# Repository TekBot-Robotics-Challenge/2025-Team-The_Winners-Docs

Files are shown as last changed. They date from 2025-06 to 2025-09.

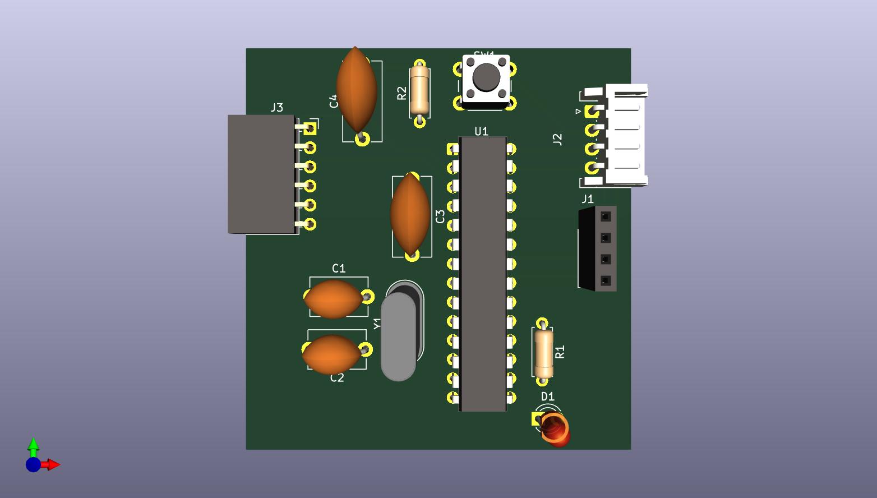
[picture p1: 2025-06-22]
Tekbot_The_Winners/electonic/test2/kicad/black_box/Test_2.jpg

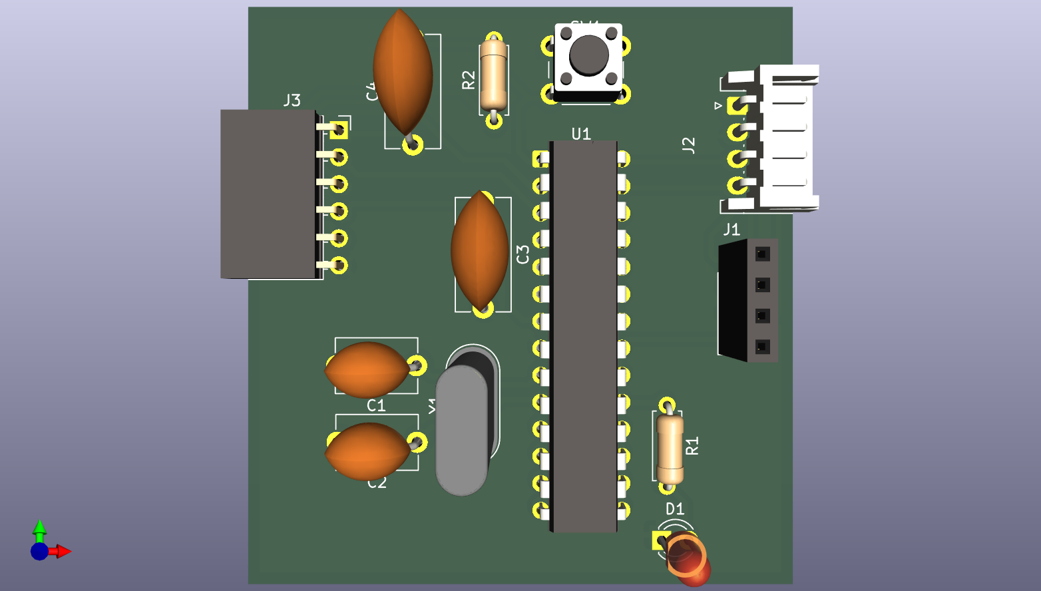
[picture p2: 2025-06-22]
Tekbot_The_Winners/electonic/test2/kicad/black_box/Test_2.png

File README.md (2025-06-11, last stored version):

# Website

This website is built using [Docusaurus](https://docusaurus.io/), a modern static website generator.

## Installation

```bash
yarn
```

## Local Development

```bash
yarn start
```

This command starts a local development server and opens up a browser window. Most changes are reflected live without having to restart the server.

## Build

```bash
yarn build
```

This command generates static content into the `build` directory and can be served using any static contents hosting service.

## Deployment

Using SSH:

```bash
USE_SSH=true yarn deploy
```

Not using SSH:

```bash
GIT_USER=<Your GitHub username> yarn deploy
```

If you are using GitHub pages for hosting, this command is a convenient way to build the website and push to the `gh-pages` branch.
"# Mise … jour" 
"Relance d‚ploiement" 
"Relance d‚ploiement"

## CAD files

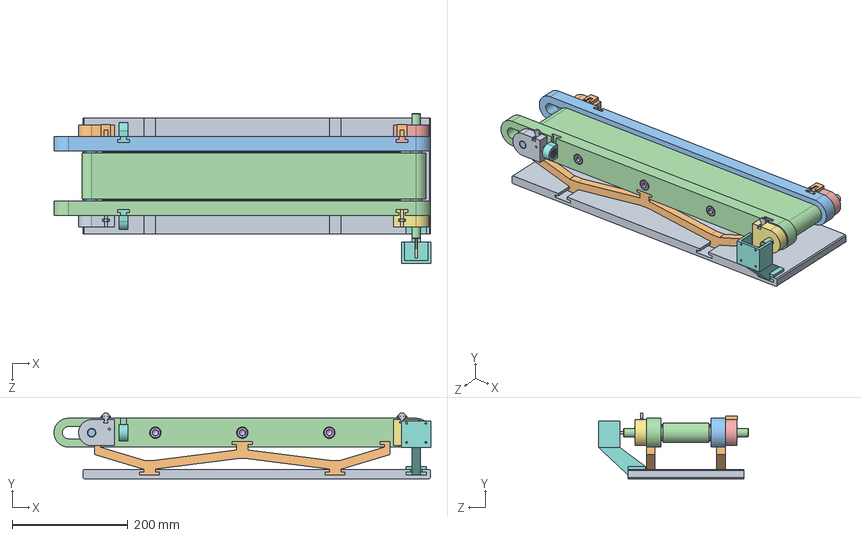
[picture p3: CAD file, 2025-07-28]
Tekbot_The_Winners/mechanic/testfinal/Assemblage2Finalconvoyeur2022.SLDASM
650.4 x 113.0 x 259.0 mm
Base
Pièce W x 2
Support lateral - Gauche
Support lateral DROIT
Palier arbre de renvoi
radial ball bearing_68_iso x 4
Palier arbre de renvoi 2
Support Tendeur 1 x 2
Palier simple coté moteur
Palier simple coté moteur 2
Tambour de renvoi
Tambour de commande
Plaque de mantient
socket head cap screw_iso x 6
Arbre du moteur
Support moteur
Boitier LDR x 2
boitier laser x 2
Dague tendeur x 2
Courroie1-1^Assemblage2Finalconvoyeur

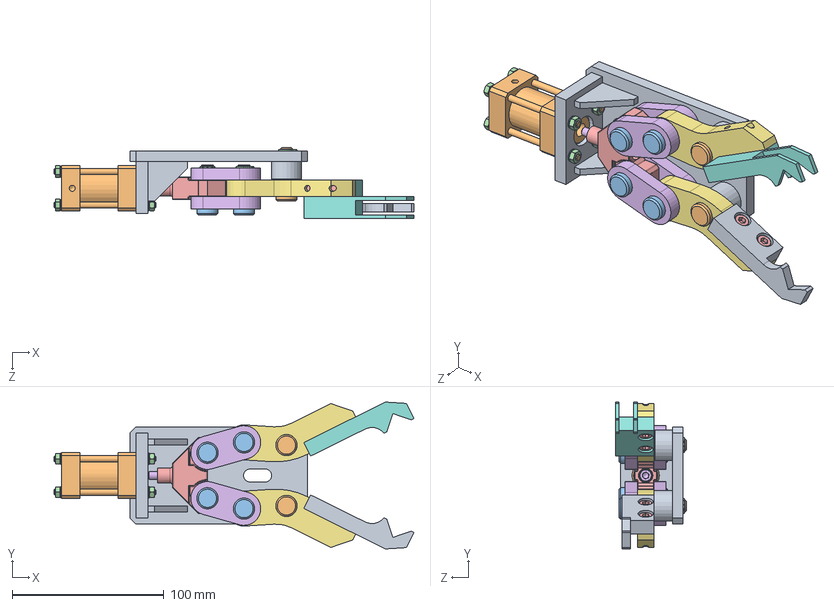
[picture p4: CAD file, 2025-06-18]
Tekbot_The_Winners/mechanic/test1/Assemblage Niveau Débutant/assemblage pince_me.SLDASM
236.9 x 96.7 x 47.0 mm
Corps
Corps verin
rondelle w4 x 8
Ecrou H M4 x 8
Embout de verin
Biellette x 4
Porte machoire x 2
Machoire gauche
Machoire droite
Axe de porte machoire x 2
Axe de biellette x 4
Circlips x 6
socket head cap screw_iso x 4
vis CHC M5x25

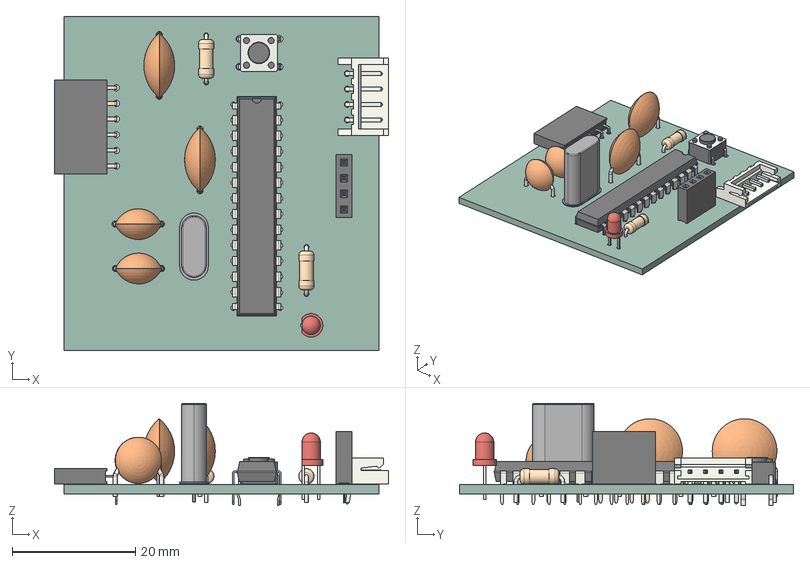
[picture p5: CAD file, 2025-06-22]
Tekbot_The_Winners/electonic/test2/kicad/black_box/Test_2.step
54.2 x 54.2 x 16.6 mm
LED_D3.0mm
JST_EH_S4B-EH_1x04_P2.50mm_Horizontal
C_Disc_D10.5mm_W5.0mm_P10.00mm x 2
PinSocket_1x04_P2.54mm_Vertical
C_Disc_D7.5mm_W5.0mm_P7.50mm x 2
R_Axial_DIN0207_L6.3mm_D2.5mm_P7.62mm_Horizontal x 2
SW_PUSH_6mm
DIP-28_W7.62mm
Crystal_HC49-U_Vertical
PinSocket_1x06_P2.54mm_Horizontal
Test_2_PCB

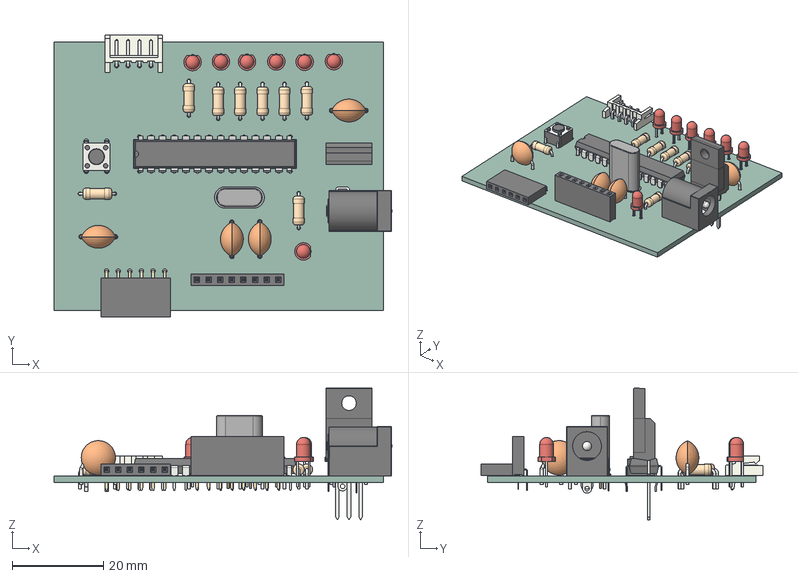
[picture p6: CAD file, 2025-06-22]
Tekbot_The_Winners/electonic/test2/kicad/station_control/Test_22.step
73.9 x 61.6 x 28.9 mm
Crystal_HC49-U_Vertical
R_Axial_DIN0207_L6.3mm_D2.5mm_P7.62mm_Horizontal x 8
SW_PUSH_6mm
C_Disc_D7.5mm_W5.0mm_P7.50mm x 4
LED_D3.0mm x 7
BarrelJack_Horizontal
PinSocket_1x08_P2.54mm_Vertical
DIP-28_W7.62mm
JST_EH_S4B-EH_1x04_P2.50mm_Horizontal
TO-220F-3_Vertical
PinSocket_1x06_P2.54mm_Horizontal
Test_22_PCB

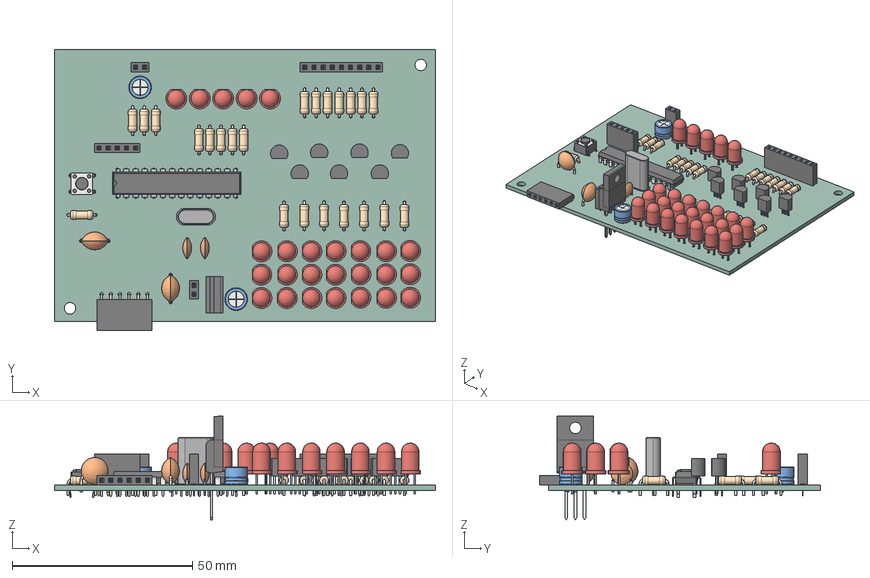
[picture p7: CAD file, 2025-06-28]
Tekbot_The_Winners/electonic/test3/KiCad/Test_3.step
105.7 x 77.9 x 28.9 mm
R_Axial_DIN0207_L6.3mm_D2.5mm_P7.62mm_Horizontal x 23
TO-92_Inline x 7
PinSocket_1x02_P2.54mm_Vertical x 2
PinSocket_1x06_P2.54mm_Horizontal
LED_D5.0mm x 26
C_Radial_D6.3mm_H5.0mm_P2.50mm x 2
C_Disc_D7.5mm_W5.0mm_P7.50mm x 2
TO-220F-3_Vertical
C_Disc_D6.0mm_W2.5mm_P5.00mm x 2
Crystal_HC49-U_Vertical
PinSocket_1x05_P2.54mm_Vertical
SW_PUSH_6mm
DIP-28_W7.62mm
PinSocket_1x09_P2.54mm_Vertical
Test_3_PCB

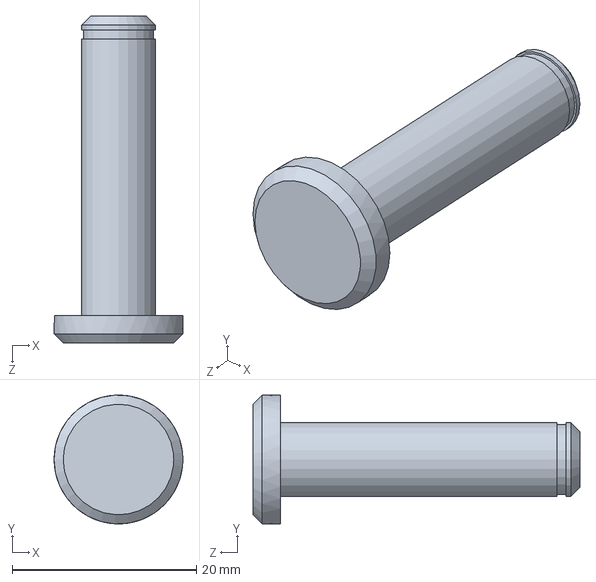
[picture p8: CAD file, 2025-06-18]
Tekbot_The_Winners/mechanic/test1/Assemblage Niveau Débutant/Axe de porte machoire.SLDPRT
14.0 x 14.0 x 35.5 mm

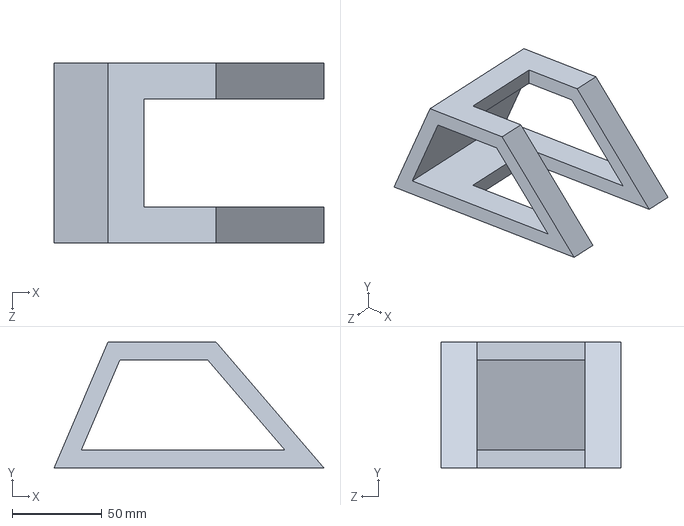
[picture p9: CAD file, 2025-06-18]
Tekbot_The_Winners/mechanic/test1/piece3.SLDPRT
150.0 x 70.0 x 100.0 mm

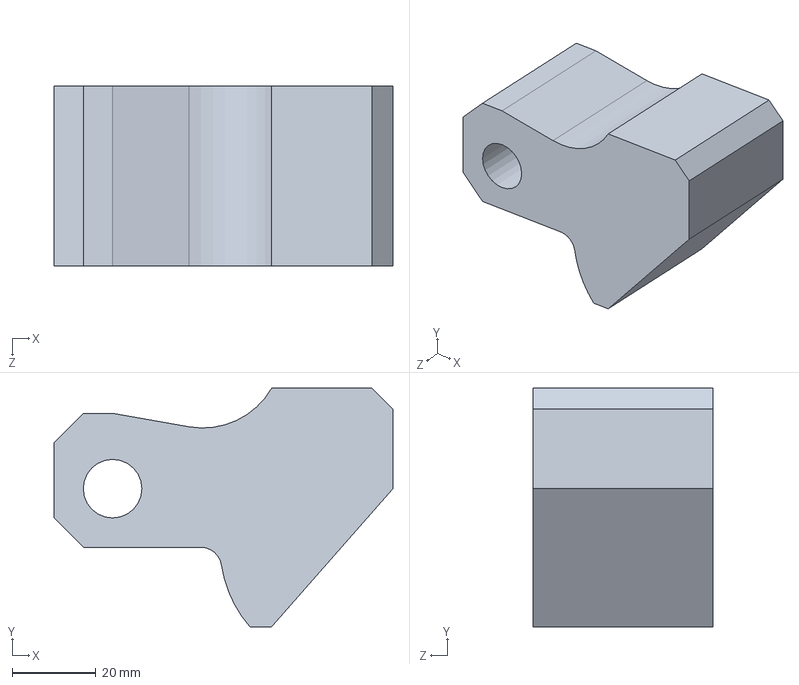
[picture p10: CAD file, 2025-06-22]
Tekbot_The_Winners/mechanic/test2/Partie1_Cas 1.SLDPRT
81.0 x 57.0 x 43.0 mm

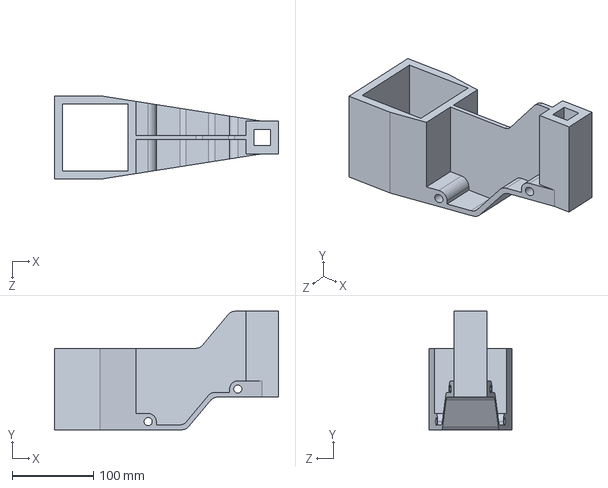
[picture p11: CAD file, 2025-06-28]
Tekbot_The_Winners/mechanic/test3/TEST3_Cas_2.SLDPRT
275.0 x 145.5 x 102.5 mm

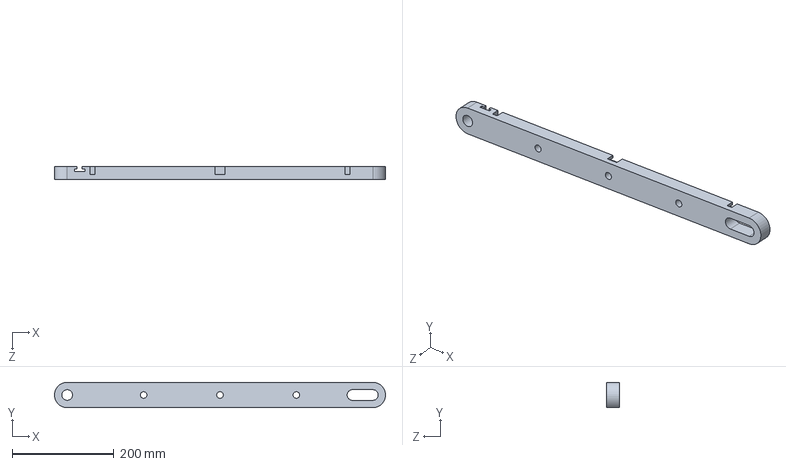
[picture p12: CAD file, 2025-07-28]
Tekbot_The_Winners/mechanic/testfinal/Support lateral - Gauche.SLDPRT
649.8 x 50.0 x 25.0 mm

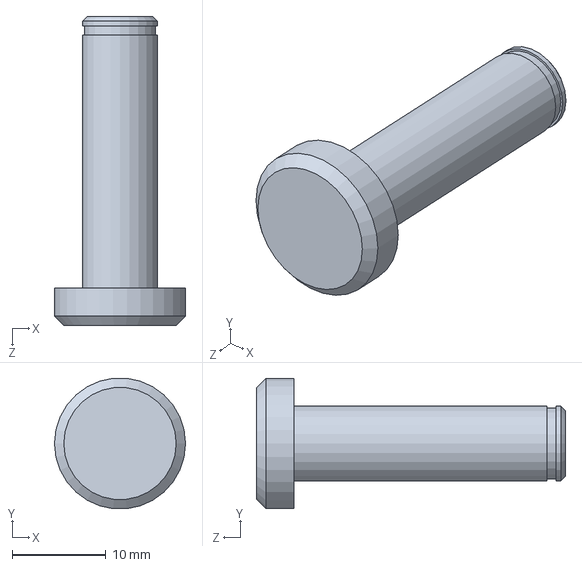
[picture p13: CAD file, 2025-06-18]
Tekbot_The_Winners/mechanic/test1/Assemblage Niveau Débutant/Axe de biellette.SLDPRT
14.0 x 13.9 x 33.0 mm

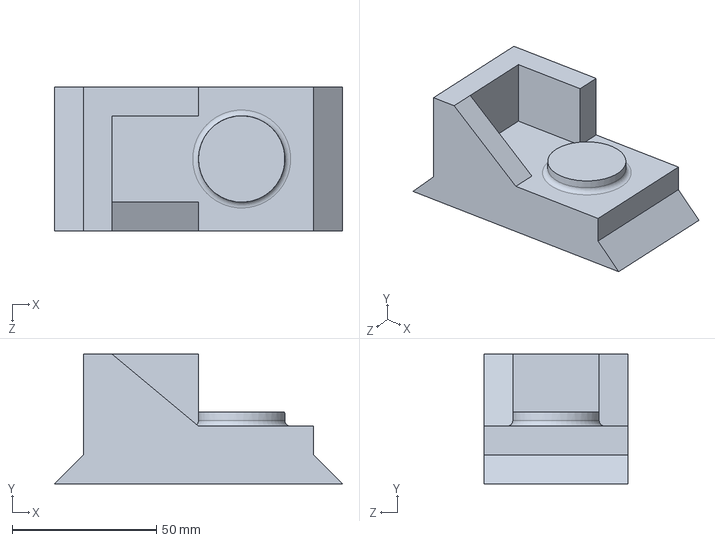
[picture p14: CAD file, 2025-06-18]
Tekbot_The_Winners/mechanic/test1/piece4.SLDPRT
100.0 x 45.0 x 50.0 mm

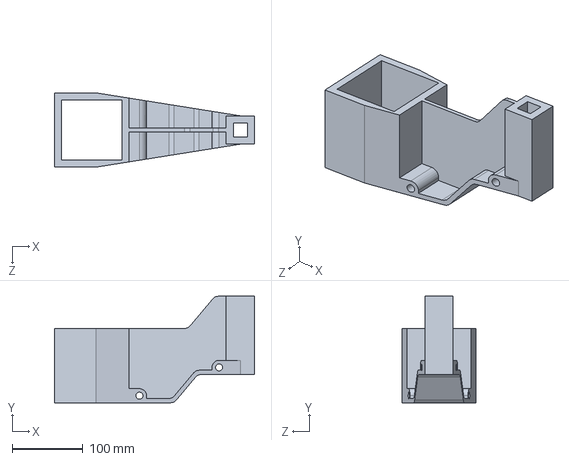
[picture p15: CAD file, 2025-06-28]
Tekbot_The_Winners/mechanic/test3/TEST3_Cas_3.SLDPRT
282.5 x 150.5 x 105.0 mm

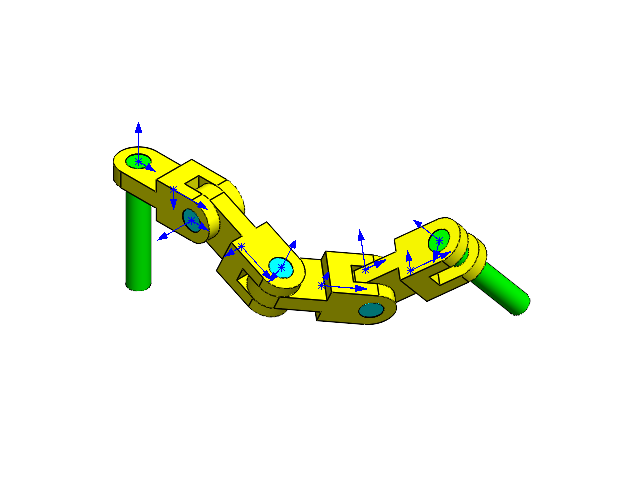
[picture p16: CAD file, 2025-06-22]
Tekbot_The_Winners/mechanic/test2/Assemblage 2_a.SLDASM
long_pin x 2
chain_link x 4
short_pin x 3

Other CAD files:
Tekbot_The_Winners/mechanic/test2/Assemblage 2_b.SLDASM
Tekbot_The_Winners/mechanic/testfinal/Moteur1.SLDASM
Tekbot_The_Winners/mechanic/test1/Assemblage Niveau Débutant/assemblage pince.SLDASM
Tekbot_The_Winners/mechanic/testfinal/Assemblage2Finalconvoyeur.SLDASM
Tekbot_The_Winners/mechanic/test1/Assemblage Niveau Débutant/Biellette.SLDPRT
Tekbot_The_Winners/mechanic/test1/Assemblage Niveau Débutant/Circlips.SLDPRT
Tekbot_The_Winners/mechanic/test1/Assemblage Niveau Débutant/Corps verin.SLDPRT
Tekbot_The_Winners/mechanic/test1/Assemblage Niveau Débutant/Corps.SLDPRT
Tekbot_The_Winners/mechanic/test1/Assemblage Niveau Débutant/Ecrou H M4.SLDPRT
Tekbot_The_Winners/mechanic/test1/Assemblage Niveau Débutant/Embout de verin.SLDPRT
Tekbot_The_Winners/mechanic/test1/Assemblage Niveau Débutant/Machoire droite.SLDPRT
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

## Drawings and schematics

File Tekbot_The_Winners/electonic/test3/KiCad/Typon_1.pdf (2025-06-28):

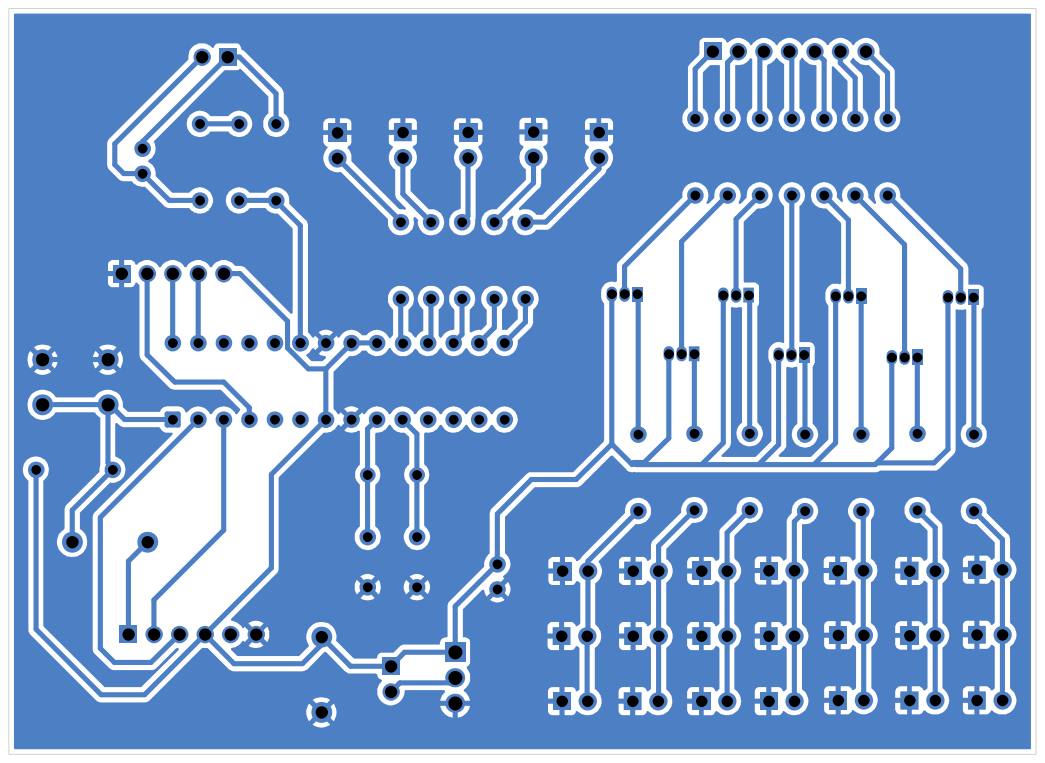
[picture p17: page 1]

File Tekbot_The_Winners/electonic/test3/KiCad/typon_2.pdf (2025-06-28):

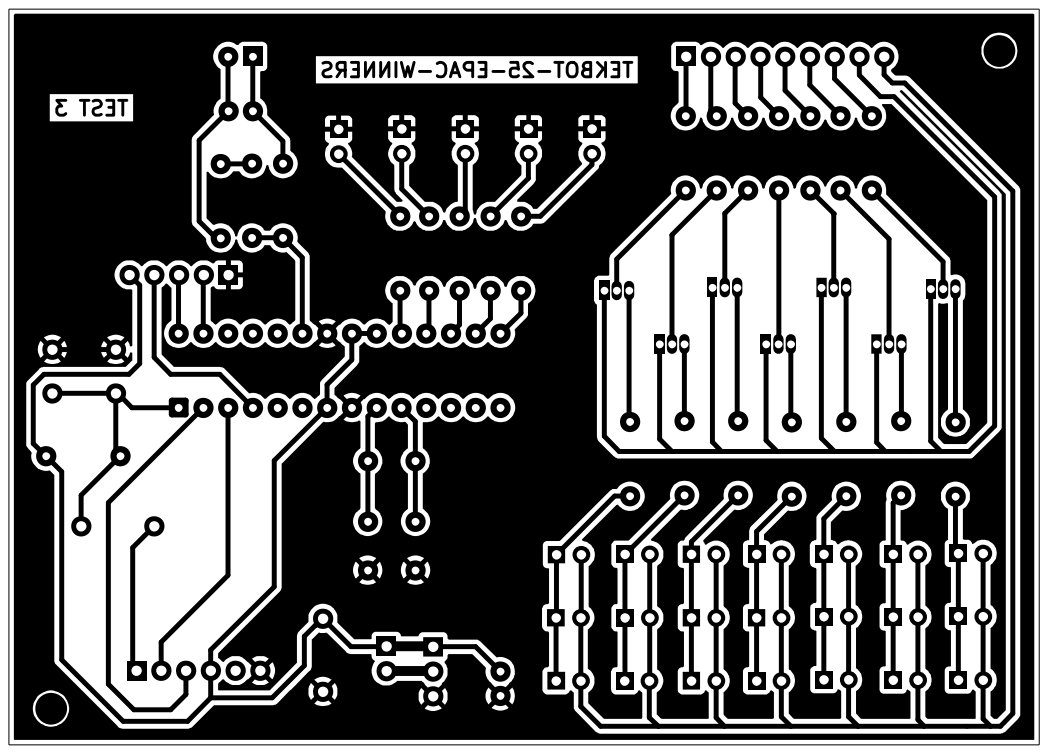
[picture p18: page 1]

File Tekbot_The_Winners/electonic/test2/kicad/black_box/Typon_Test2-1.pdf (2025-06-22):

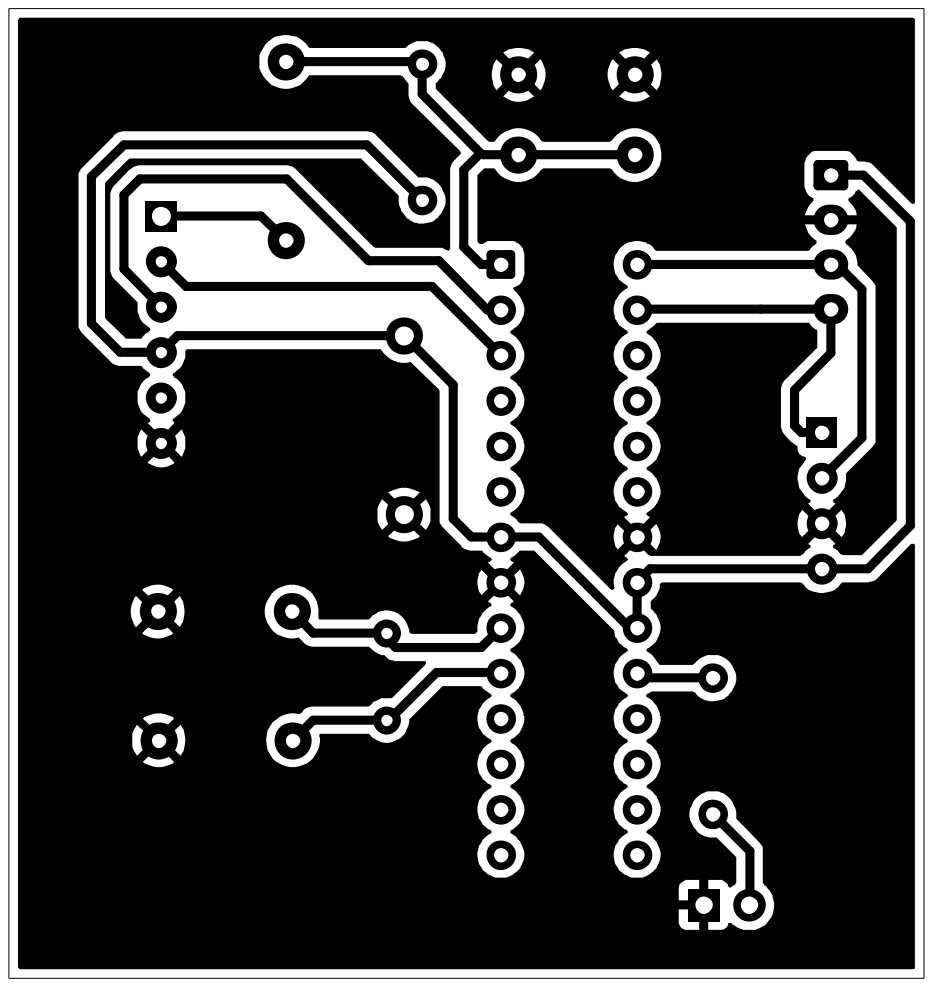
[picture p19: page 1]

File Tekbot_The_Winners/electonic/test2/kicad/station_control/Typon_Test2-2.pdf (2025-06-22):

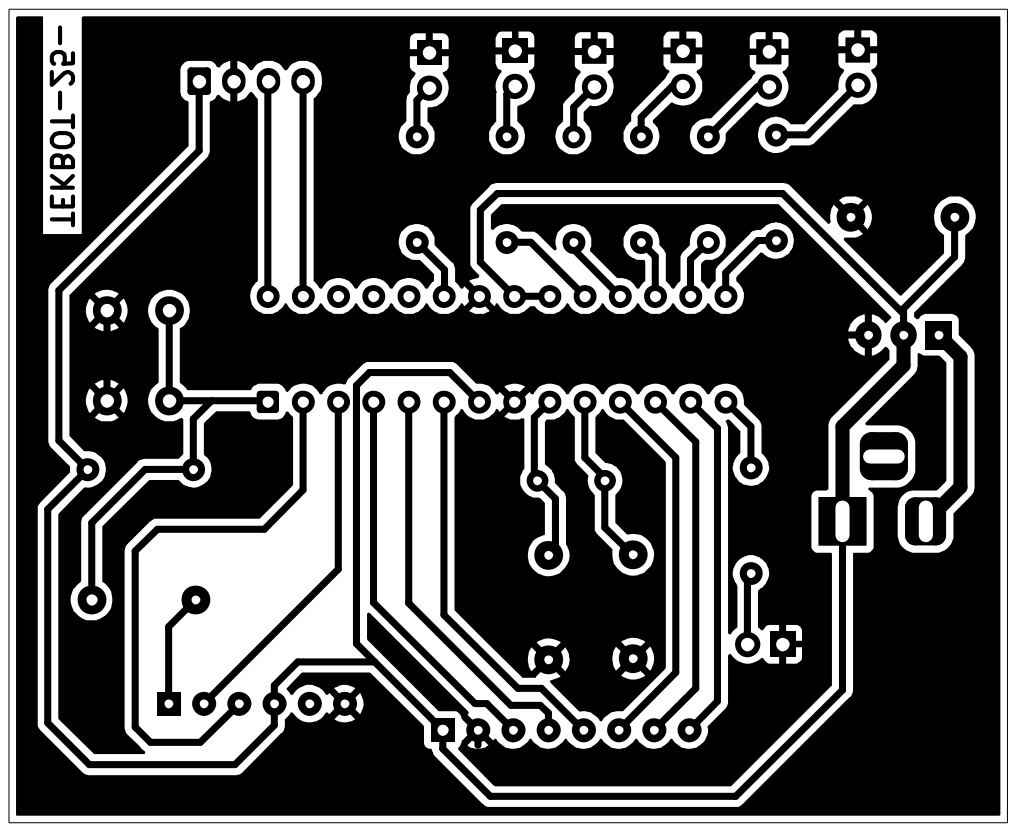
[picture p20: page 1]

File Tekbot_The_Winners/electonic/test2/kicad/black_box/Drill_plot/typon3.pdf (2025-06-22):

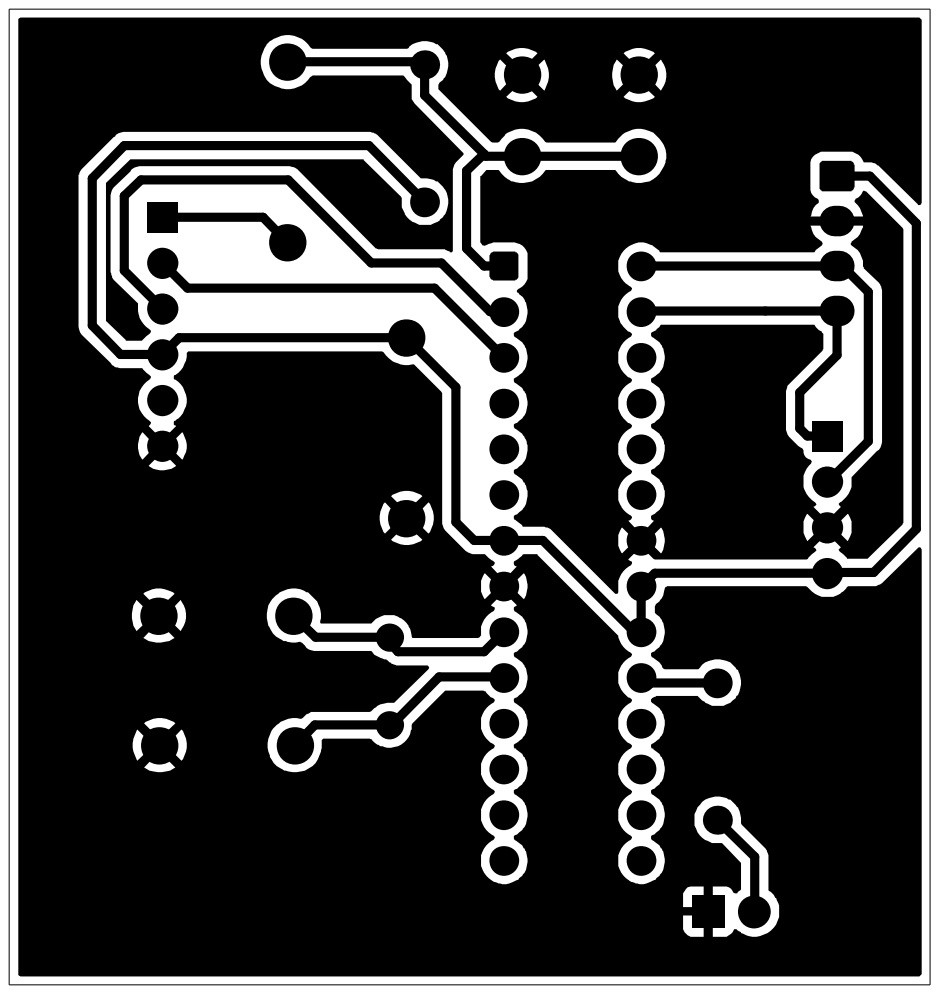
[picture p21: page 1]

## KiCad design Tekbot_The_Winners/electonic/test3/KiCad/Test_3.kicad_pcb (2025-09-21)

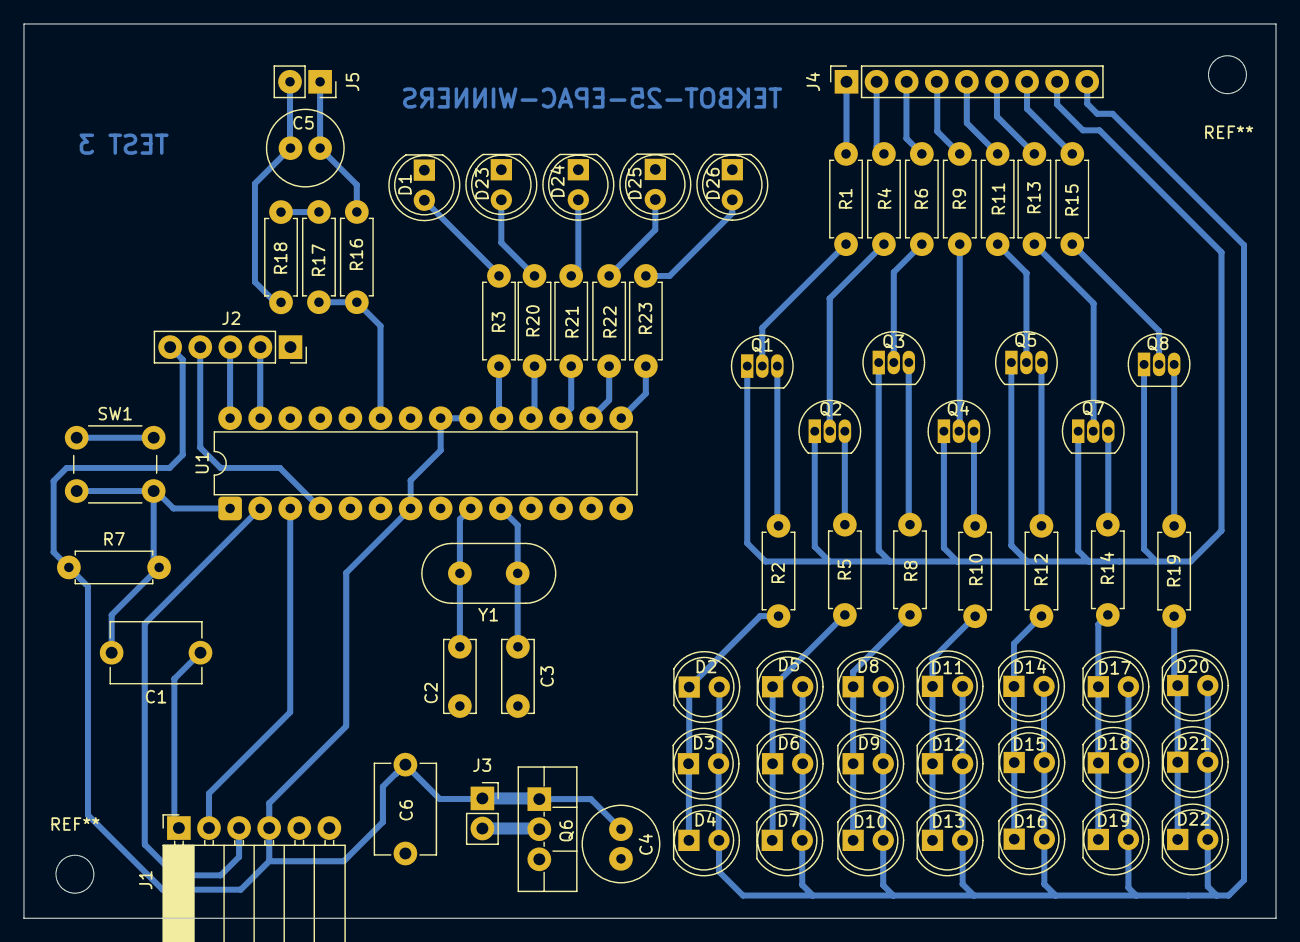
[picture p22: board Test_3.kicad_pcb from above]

Board: 2 copper layers, 105.7 x 75.5 mm, 71 parts (0 on the bottom side), 56 nets.

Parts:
C1: 100nF; C_Disc_D7.5mm_W5.0mm_P7.50mm
C2, C3: 22pF; C_Disc_D6.0mm_W2.5mm_P5.00mm
C4, C5: 470µF; C_Radial_D6.3mm_H5.0mm_P2.50mm
C6: 100n; C_Disc_D7.5mm_W5.0mm_P7.50mm
D1, D2, D3, D4, D5, D6, D7, D8, D9, D10, D11, D12, D13, D14, D15, D16, D17, D18, D19, D20, D21, D22, D23, D24, D25, D26: LED; LED_D5.0mm
J1: Prog_connector; PinSocket_1x06_P2.54mm_Horizontal
J2: Conn_01x05_Pin; PinSocket_1x05_P2.54mm_Vertical
J3: 5V_power_Pins; PinSocket_1x02_P2.54mm_Vertical
J4: LED_pwm_connector; PinSocket_1x09_P2.54mm_Vertical
J5: Batt_connector; PinSocket_1x02_P2.54mm_Vertical
Q1, Q2, Q3, Q4, Q5, Q7, Q8: 2N2219; TO-92_Inline
Q6: NMOS; TO-220F-3_Vertical
R1, R2, R4, R5, R6, R8, R9, R10, R11, R12, R13, R14, R15, R19, R20, R21, R22, R23: R; R_Axial_DIN0207_L6.3mm_D2.5mm_P7.62mm_Horizontal
R3: 220; R_Axial_DIN0207_L6.3mm_D2.5mm_P7.62mm_Horizontal
R7, R16, R17: 10k; R_Axial_DIN0207_L6.3mm_D2.5mm_P7.62mm_Horizontal
R18: 4.7k; R_Axial_DIN0207_L6.3mm_D2.5mm_P7.62mm_Horizontal
SW1: SW_Push; SW_PUSH_6mm
U1: ATmega328-P; DIP-28_W7.62mm
Y1: Crystal; Crystal_HC49-U_Vertical

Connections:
/B+: C5.1, J5.1, R16.1
/B-: C5.2, J5.2, R18.2
/L_GND: J4.8, Q1.1 (E), Q2.1 (E), Q3.1 (E), Q4.1 (E), Q5.1 (E), Q7.1 (E), Q8.1 (E)
/L_Vcc: D2.2 (A), D3.2 (A), D4.2 (A), D5.2 (A), D6.2 (A), D7.2 (A), D8.2 (A), D9.2 (A), D10.2 (A), D11.2 (A), D12.2 (A), D13.2 (A), D14.2 (A), D15.2 (A), D16.2 (A), D17.2 (A), D18.2 (A), D19.2 (A), D20.2 (A), D21.2 (A), D22.2 (A), J4.9
/sg1: J4.1, R1.1
/sg2: J4.2, R4.1
/sg3: J4.3, R6.1
/sg4: J4.4, R9.1
/sg5: J4.5, R11.1
/sg6: J4.6, R13.1
/sg7: J4.7, R15.1
A0: R16.2, R17.1, U1.23 (PC0)
GND: J3.2, Q6.2 (D)
L-25: R23.1, U1.15 (PB1)
L-50: R22.1, U1.16 (PB2)
L-75: R21.1, U1.17 (PB3)
L-100: R20.1, U1.18 (PB4)
Lbuilt: R3.1, U1.19 (PB5)
unnamed: D1.2 (A), R3.2
unnamed: D2.1 (K), D3.1 (K), D4.1 (K), R2.2
unnamed: D5.1 (K), D6.1 (K), D7.1 (K), R5.2
unnamed: D8.1 (K), D9.1 (K), D10.1 (K), R8.2
unnamed: D11.1 (K), D12.1 (K), D13.1 (K), R10.2
unnamed: D14.1 (K), D15.1 (K), D16.1 (K), R12.2
unnamed: D17.1 (K), D18.1 (K), D19.1 (K), R14.2
unnamed: D20.1 (K), D21.1 (K), D22.1 (K), R19.2
unnamed: D23.2 (A), R20.2
unnamed: D24.2 (A), R21.2
unnamed: D25.2 (A), R22.2
unnamed: D26.2 (A), R23.2
unnamed: C1.1, J1.1
unnamed: Q1.2 (B), R1.2
unnamed: Q1.3 (C), R2.1
unnamed: Q2.2 (B), R4.2
unnamed: Q2.3 (C), R5.1
unnamed: Q3.2 (B), R6.2
unnamed: Q3.3 (C), R8.1
unnamed: Q4.2 (B), R9.2
unnamed: Q4.3 (C), R10.1
unnamed: Q5.2 (B), R11.2
unnamed: Q5.3 (C), R12.1
unnamed: Q7.2 (B), R13.2
unnamed: Q7.3 (C), R14.1
unnamed: Q8.2 (B), R15.2
unnamed: Q8.3 (C), R19.1
unnamed: R17.2, R18.1
OE: J2.4, U1.4 (PD2)
RST: C1.2, R7.2, SW1.2, U1.1 (~RESET/PC6)
Rx: J1.2, U1.3 (PD1)
SCL: J2.3, U1.28 (PC5)
SDA: J2.2, U1.27 (PC4)
Tx: J1.3, U1.2 (PD0)
V+: C4.1, C6.1, J1.4, J2.5, J3.1, Q6.1 (G), R7.1, U1.7 (VCC), U1.20 (AVCC), U1.21 (AREF)
V-: C2.2, C3.2, C4.2, C6.2, D1.1 (K), D23.1 (K), D24.1 (K), D25.1 (K), D26.1 (K), J1.6, J2.1, Q6.3 (S), SW1.1, U1.8 (GND), U1.22 (GND)
XTAL1: C2.1, U1.9 (XTAL1/PB6), Y1.2
XTAL2: C3.1, U1.10 (XTAL2/PB7), Y1.1

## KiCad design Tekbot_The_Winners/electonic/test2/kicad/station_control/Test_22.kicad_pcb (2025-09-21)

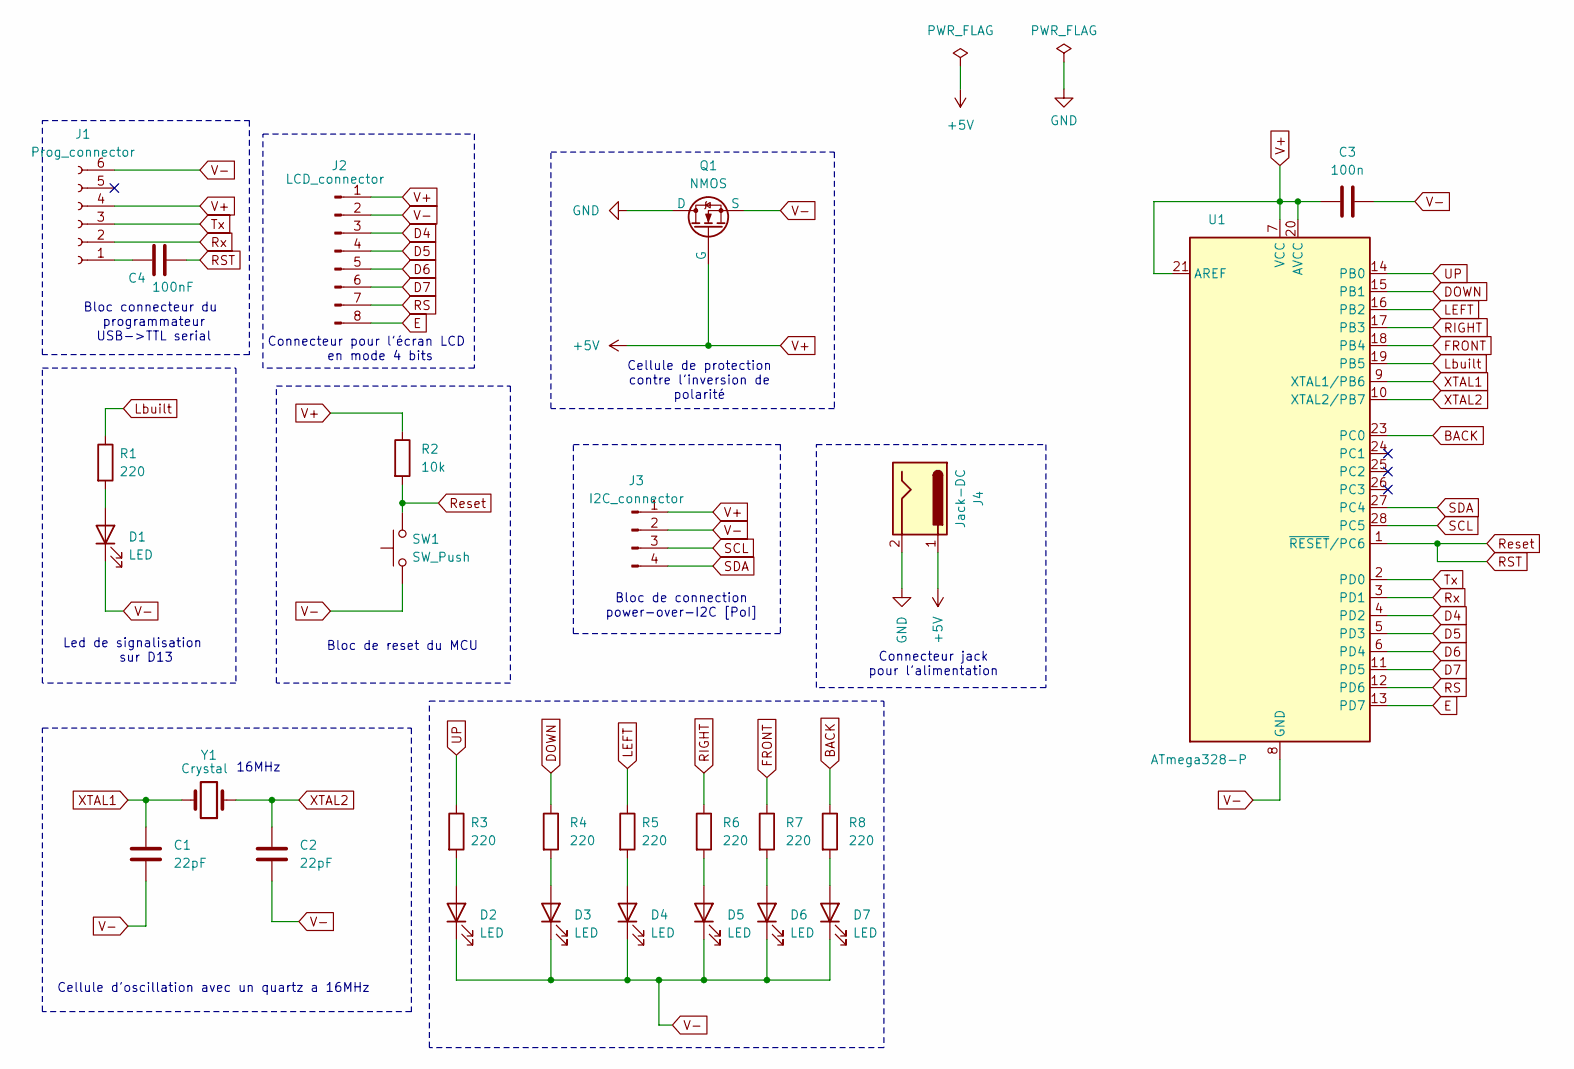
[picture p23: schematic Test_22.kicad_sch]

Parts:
C1, C2: 22pF; C_Disc_D7.5mm_W5.0mm_P7.50mm
C3: 100n; C_Disc_D7.5mm_W5.0mm_P7.50mm
C4: 100nF; C_Disc_D7.5mm_W5.0mm_P7.50mm
D1, D2, D3, D4, D5, D6, D7: LED; LED_D3.0mm
J1: Prog_connector; PinSocket_1x06_P2.54mm_Horizontal
J2: LCD_connector; PinSocket_1x08_P2.54mm_Vertical
J3: I2C_connector; JST_EH_S4B-EH_1x04_P2.50mm_Horizontal
J4: Jack-DC; BarrelJack_Horizontal
Q1: NMOS; TO-220F-3_Vertical
R1, R3, R4, R5, R6, R7, R8: 220; R_Axial_DIN0207_L6.3mm_D2.5mm_P7.62mm_Horizontal
R2: 10k; R_Axial_DIN0207_L6.3mm_D2.5mm_P7.62mm_Horizontal
SW1: SW_Push; SW_PUSH_6mm
U1: ATmega328-P; DIP-28_W7.62mm
Y1: Crystal; Crystal_HC49-U_Vertical

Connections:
BACK: R8.1, U1.23 (PC0)
D4: J2.3, U1.4 (PD2)
D5: J2.4, U1.5 (PD3)
D6: J2.5, U1.6 (PD4)
D7: J2.6, U1.11 (PD5)
DOWN: R4.1, U1.15 (PB1)
E: J2.8, U1.13 (PD7)
FRONT: R7.1, U1.18 (PB4)
GND: J4.2, Q1.1 (D)
LEFT: R5.1, U1.16 (PB2)
Lbuilt: R1.1, U1.19 (PB5)
unnamed: D1.2 (A), R1.2
unnamed: D2.2 (A), R3.2
unnamed: D3.2 (A), R4.2
unnamed: D4.2 (A), R5.2
unnamed: D5.2 (A), R6.2
unnamed: D6.2 (A), R7.2
unnamed: D7.2 (A), R8.2
unnamed: C4.1, J1.1
RIGHT: R6.1, U1.17 (PB3)
RS: J2.7, U1.12 (PD6)
RST: C4.2, R2.2, SW1.2, U1.1 (~RESET/PC6)
Rx: J1.2, U1.3 (PD1)
SCL: J3.3, U1.28 (PC5)
SDA: J3.4, U1.27 (PC4)
Tx: J1.3, U1.2 (PD0)
UP: R3.1, U1.14 (PB0)
V+: C3.1, J1.4, J2.1, J3.1, J4.1, Q1.2 (G), R2.1, U1.7 (VCC), U1.20 (AVCC), U1.21 (AREF)
V-: C1.2, C2.2, C3.2, D1.1 (K), D2.1 (K), D3.1 (K), D4.1 (K), D5.1 (K), D6.1 (K), D7.1 (K), J1.6, J2.2, J3.2, Q1.3 (S), SW1.1, U1.8 (GND), U1.22 (GND)
XTAL1: C1.1, U1.9 (XTAL1/PB6), Y1.2
XTAL2: C2.1, U1.10 (XTAL2/PB7), Y1.1

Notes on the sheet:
16MHz
Bloc connecteur du programmateur USB->TTL serial
Bloc de reset du MCU
Bloc de connection power-over-I2C [PoI]
Led de signalisation sur D13
Cellule d'oscillation avec un quartz a 16MHz
Connecteur jack pour l'alimentation
Cellule de protection contre l'inversion de polarité
Connecteur pour l'écran LCD en mode 4 bits

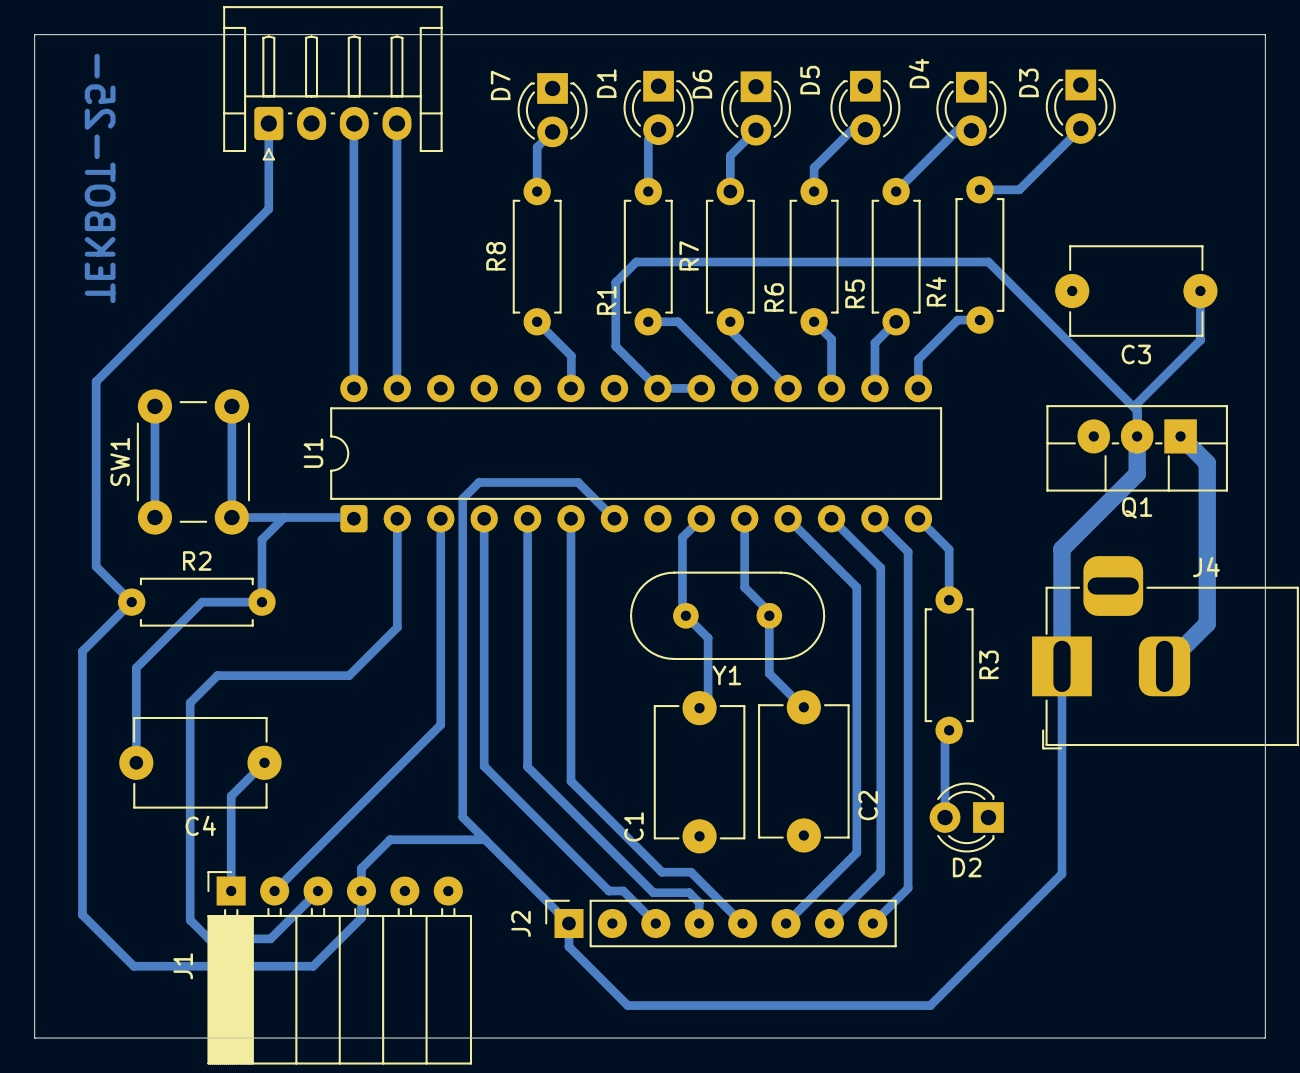
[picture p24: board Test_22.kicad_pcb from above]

Board: 2 copper layers, 72.0 x 58.7 mm, 27 parts (0 on the bottom side), 31 nets.

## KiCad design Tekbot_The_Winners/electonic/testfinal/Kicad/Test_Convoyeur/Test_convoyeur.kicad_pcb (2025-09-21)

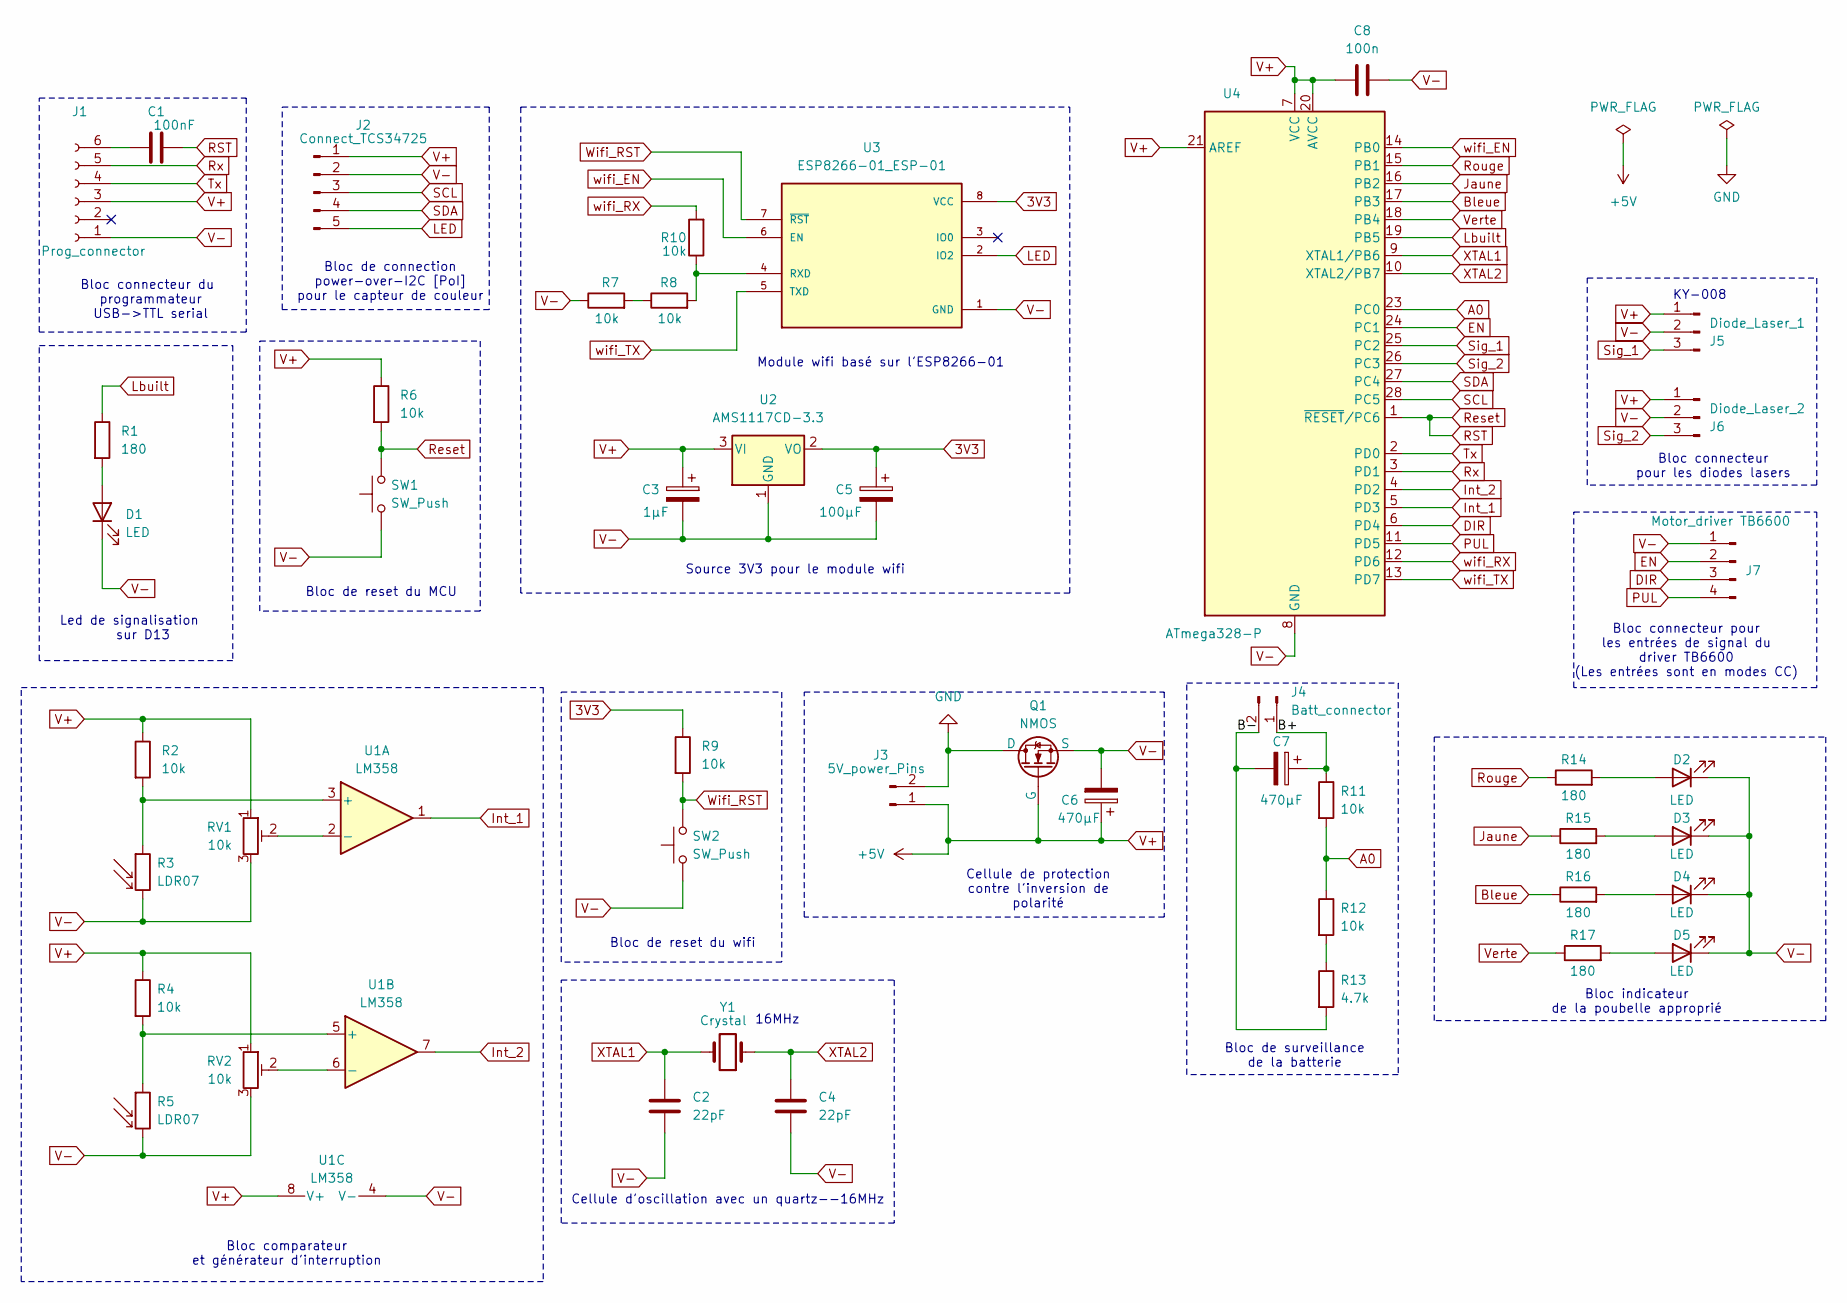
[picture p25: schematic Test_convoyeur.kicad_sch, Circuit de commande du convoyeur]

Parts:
C1: 100nF; C_Disc_D7.5mm_W5.0mm_P7.50mm
C2, C4: 22pF; C_Disc_D6.0mm_W2.5mm_P5.00mm
C3: 1µF; C_Radial_D6.3mm_H5.0mm_P2.50mm
C5: 100µF; C_Radial_D6.3mm_H5.0mm_P2.50mm
C6, C7: 470µF; C_Radial_D6.3mm_H5.0mm_P2.50mm
C8: 100n; C_Disc_D7.5mm_W5.0mm_P7.50mm
D1, D2, D3, D4, D5: LED; LED_D5.0mm
J1: Prog_connector; PinSocket_1x06_P2.54mm_Horizontal
J2: Connect_TCS34725; PinSocket_1x05_P2.54mm_Vertical
J3: 5V_power_Pins; PinSocket_1x02_P2.54mm_Vertical
J4: Batt_connector; PinSocket_1x02_P2.54mm_Vertical
J5: Diode_Laser_1; PinSocket_1x03_P2.54mm_Vertical
J6: Diode_Laser_2; PinSocket_1x03_P2.54mm_Vertical
J7: Motor_driver TB6600; PinHeader_1x04_P2.54mm_Vertical
Q1: NMOS; TO-220F-3_Vertical
R1, R14, R15, R16, R17: 180; R_Axial_DIN0207_L6.3mm_D2.5mm_P10.16mm_Horizontal
R2, R4, R6, R7, R8, R9, R10, R11, R12: 10k; R_Axial_DIN0207_L6.3mm_D2.5mm_P10.16mm_Horizontal
R3, R5: LDR07; R_LDR_5.1x4.3mm_P3.4mm_Vertical
R13: 4.7k; R_Axial_DIN0207_L6.3mm_D2.5mm_P10.16mm_Horizontal
RV1, RV2: 10k; R_ajustable
SW1, SW2: SW_Push; SW_PUSH_6mm
U1: LM358; DIP-8_W7.62mm
U2: AMS1117CD-3.3; TO-252-3_TabPin2
U3: ESP8266-01_ESP-01; XCVR_ESP8266-01_ESP-01; PARTREV V1.2
U4: ATmega328-P; DIP-28_W7.62mm
Y1: Crystal; Crystal_HC49-U_Vertical

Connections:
3V3: C5.1, R9.1, U2.2 (VO), U3.8 (VCC)
/B+: C7.1, J4.1, R11.1
/B-: C7.2, J4.2, R13.2
A0: R11.2, R12.1, U4.23 (PC0)
Bleue: R16.1, U4.17 (PB3)
DIR: J7.3, U4.6 (PD4)
EN: J7.2, U4.24 (PC1)
GND: J3.2, Q1.2 (D)
Int_1: U1.1, U4.5 (PD3)
Int_2: U1.7, U4.4 (PD2)
Jaune: R15.1, U4.16 (PB2)
LED: J2.5, U3.2 (IO2)
Lbuilt: R1.1, U4.19 (PB5)
unnamed: D1.2 (A), R1.2
unnamed: D2.2 (A), R14.2
unnamed: D3.2 (A), R15.2
unnamed: D4.2 (A), R16.2
unnamed: D5.2 (A), R17.2
unnamed: C1.1, J1.6
unnamed: R7.2, R8.1
unnamed: R12.2, R13.1
unnamed: R2.2, R3.1, U1.3 (+)
unnamed: RV1.2, U1.2 (-)
unnamed: R4.2, R5.1, U1.5 (+)
unnamed: RV2.2, U1.6 (-)
unnamed: R8.2, R10.1, U3.4 (RXD)
PUL: J7.4, U4.11 (PD5)
RST: C1.2, R6.2, SW1.2, U4.1 (~RESET/PC6)
Rouge: R14.1, U4.15 (PB1)
Rx: J1.5, U4.3 (PD1)
SCL: J2.3, U4.28 (PC5)
SDA: J2.4, U4.27 (PC4)
Sig_1: J5.3, U4.25 (PC2)
Sig_2: J6.3, U4.26 (PC3)
Tx: J1.4, U4.2 (PD0)
V+: C3.1, C6.1, C8.1, J1.3, J2.1, J3.1, J5.1, J6.1, Q1.1 (G), R2.1, R4.1, R6.1, RV1.1, RV2.1, U1.8 (V+), U2.3 (VI), U4.7 (VCC), U4.20 (AVCC), U4.21 (AREF)
V-: C2.2, C3.2, C4.2, C5.2, C6.2, C8.2, D1.1 (K), D2.1 (K), D3.1 (K), D4.1 (K), D5.1 (K), J1.1, J2.2, J5.2, J6.2, J7.1, Q1.3 (S), R3.2, R5.2, R7.1, RV1.3, RV2.3, SW1.1, SW2.1, U1.4 (V-), U2.1 (GND), U3.1 (GND), U4.8 (GND), U4.22 (GND)
Verte: R17.1, U4.18 (PB4)
Wifi_RST: R9.2, SW2.2, U3.7 (~RST)
XTAL1: C2.1, U4.9 (XTAL1/PB6), Y1.2
XTAL2: C4.1, U4.10 (XTAL2/PB7), Y1.1
wifi_EN: U3.6 (EN), U4.14 (PB0)
wifi_RX: R10.2, U4.12 (PD6)
wifi_TX: U3.5 (TXD), U4.13 (PD7)

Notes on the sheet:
Cellule de protection contre l'inversion de polarité
Bloc de reset du MCU
Bloc connecteur pour les entrées de signal du driver TB6600 (Les entrées sont en modes CC)
Bloc comparateur et générateur d'interruption
Source 3V3 pour le module wifi
Bloc indicateur de la poubelle approprié
Bloc de reset du wifi
Module wifi basé sur l'ESP8266-01
16MHz
KY-008
Bloc de surveillance de la batterie
Led de signalisation sur D13
Bloc connecteur pour les diodes lasers
Bloc de connection power-over-I2C [PoI] pour le capteur de couleur
Bloc connecteur du programmateur USB->TTL serial
Cellule d'oscillation avec un quartz--16MHz

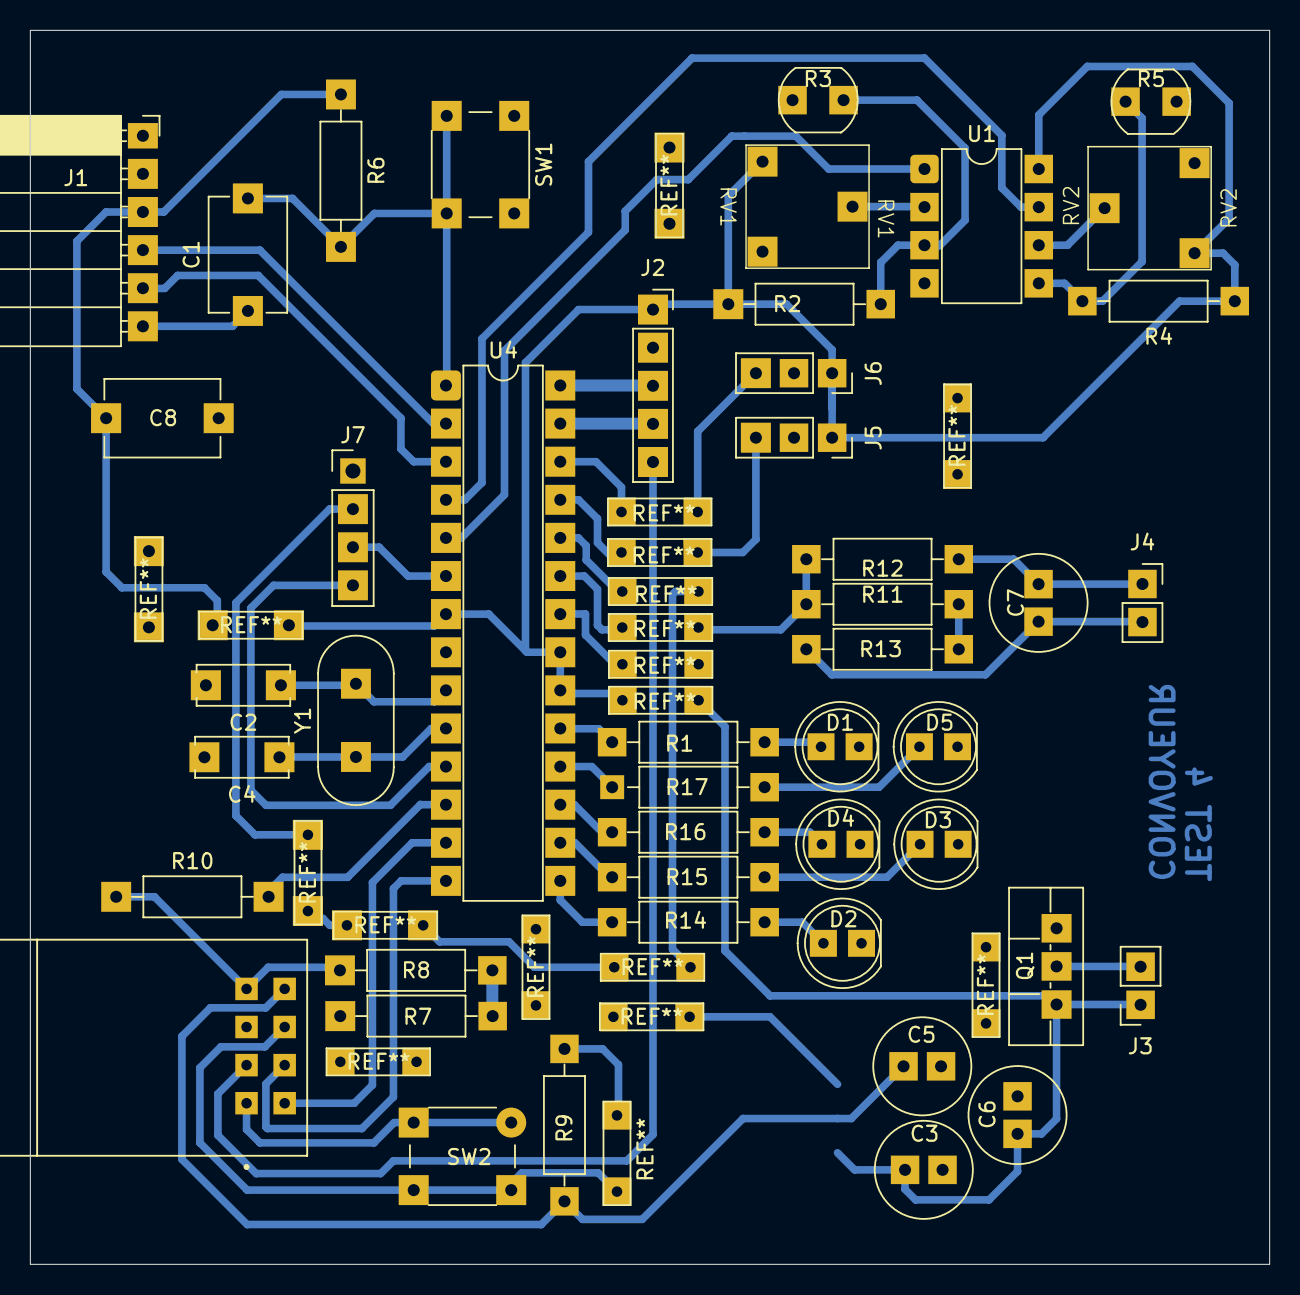
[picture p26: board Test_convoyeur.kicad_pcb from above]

Board: 2 copper layers, 82.6 x 82.2 mm, 47 parts (1 on the bottom side), 44 nets.

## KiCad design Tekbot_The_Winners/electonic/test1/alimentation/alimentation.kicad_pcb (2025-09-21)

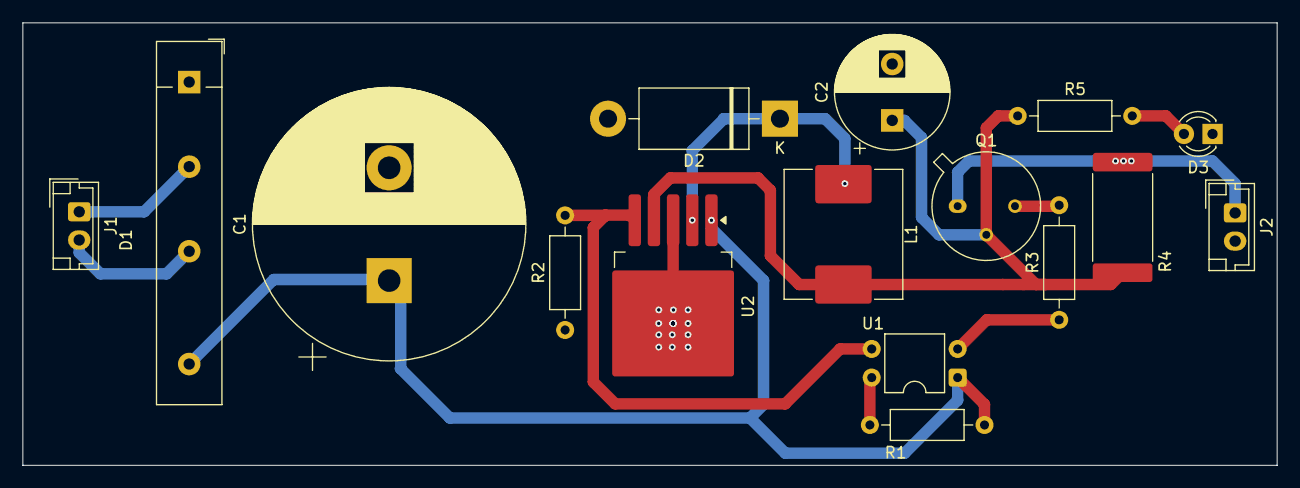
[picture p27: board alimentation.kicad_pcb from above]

Board: 2 copper layers, 111.2 x 39.2 mm, 16 parts (0 on the bottom side), 12 nets.

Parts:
C1: 4700µF; CP_Radial_D24.0mm_P10.00mm_SnapIn
C2: 470µF; CP_Radial_D10.0mm_P5.00mm
D1: B40C5000-3x00A; Diode_Bridge_32.0x5.6x17.0mm_P10.0mm_P7.5mm
D2: 1N5822; D_DO-201AD_P15.24mm_Horizontal
D3: LED; LED_D3.0mm
J1: Input; JST_EH_B2B-EH-A_1x02_P2.50mm_Vertical
J2: Output; JST_EH_B2B-EH-A_1x02_P2.50mm_Vertical
L1: 33µH; L_Bourns_SRP1050WA
Q1: 2N2219; TO-39-3
R1, R2: 10k; R_Axial_DIN0207_L6.3mm_D2.5mm_P10.16mm_Horizontal
R3: 180; R_Axial_DIN0207_L6.3mm_D2.5mm_P10.16mm_Horizontal
R4: 350m; R_4020_10251Metric_Pad1.65x5.30mm_HandSolder
R5: 150; R_Axial_DIN0207_L6.3mm_D2.5mm_P10.16mm_Horizontal
U1: PC817; DIP-4_W7.62mm
U2: LM2596S-5; TO-263-5_TabPin3

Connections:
GND: C1.2, C2.2, D1.1 (-), D2.2 (A), D3.1 (K), J2.2, R2.1, U2.3 (GND)
unnamed: D2.1 (K), L1.1, U2.2 (OUT)
unnamed: D3.2 (A), R5.2
unnamed: Q1.3 (C), R3.2
unnamed: R1.1, U1.4
unnamed: R3.1, U1.2
S1: D1.2, J1.1
S2: D1.3, J1.2
Vin: C1.1, D1.4 (+), R1.2, U1.1, U2.1 (VIN)
Vo: C2.1, L1.2, Q1.2 (B), R4.1, R5.1, U2.4 (FB)
Von_off: R2.2, U1.3, U2.5 (~ON/OFF)
Vout: J2.1, Q1.1 (E), R4.2

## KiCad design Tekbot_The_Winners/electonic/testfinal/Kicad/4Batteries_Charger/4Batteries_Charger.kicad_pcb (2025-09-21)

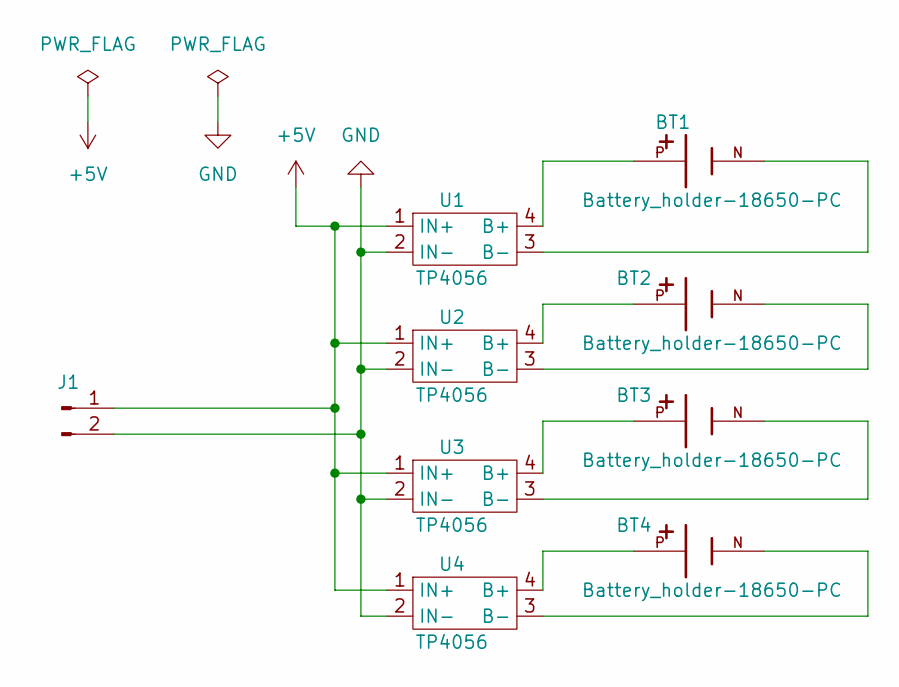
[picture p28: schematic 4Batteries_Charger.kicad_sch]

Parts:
BT1, BT2, BT3, BT4: Battery_holder-18650-PC; BAT_holder-18650-PC; PARTREV 05/17/19
J1: Conn_01x02_Pin; JST_EH_B2B-EH-A_1x02_P2.50mm_Vertical
U1, U2, U3, U4: TP4056; TP4056_module

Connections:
+5V: J1.1, U1.1 (IN+), U2.1 (IN+), U3.1 (IN+), U4.1 (IN+)
GND: J1.2, U1.2 (IN-), U2.2 (IN-), U3.2 (IN-), U4.2 (IN-)
unnamed: BT1.P, U1.4 (B+)
unnamed: BT1.N, U1.3 (B-)
unnamed: BT2.P, U2.4 (B+)
unnamed: BT2.N, U2.3 (B-)
unnamed: BT3.P, U3.4 (B+)
unnamed: BT3.N, U3.3 (B-)
unnamed: BT4.P, U4.4 (B+)
unnamed: BT4.N, U4.3 (B-)

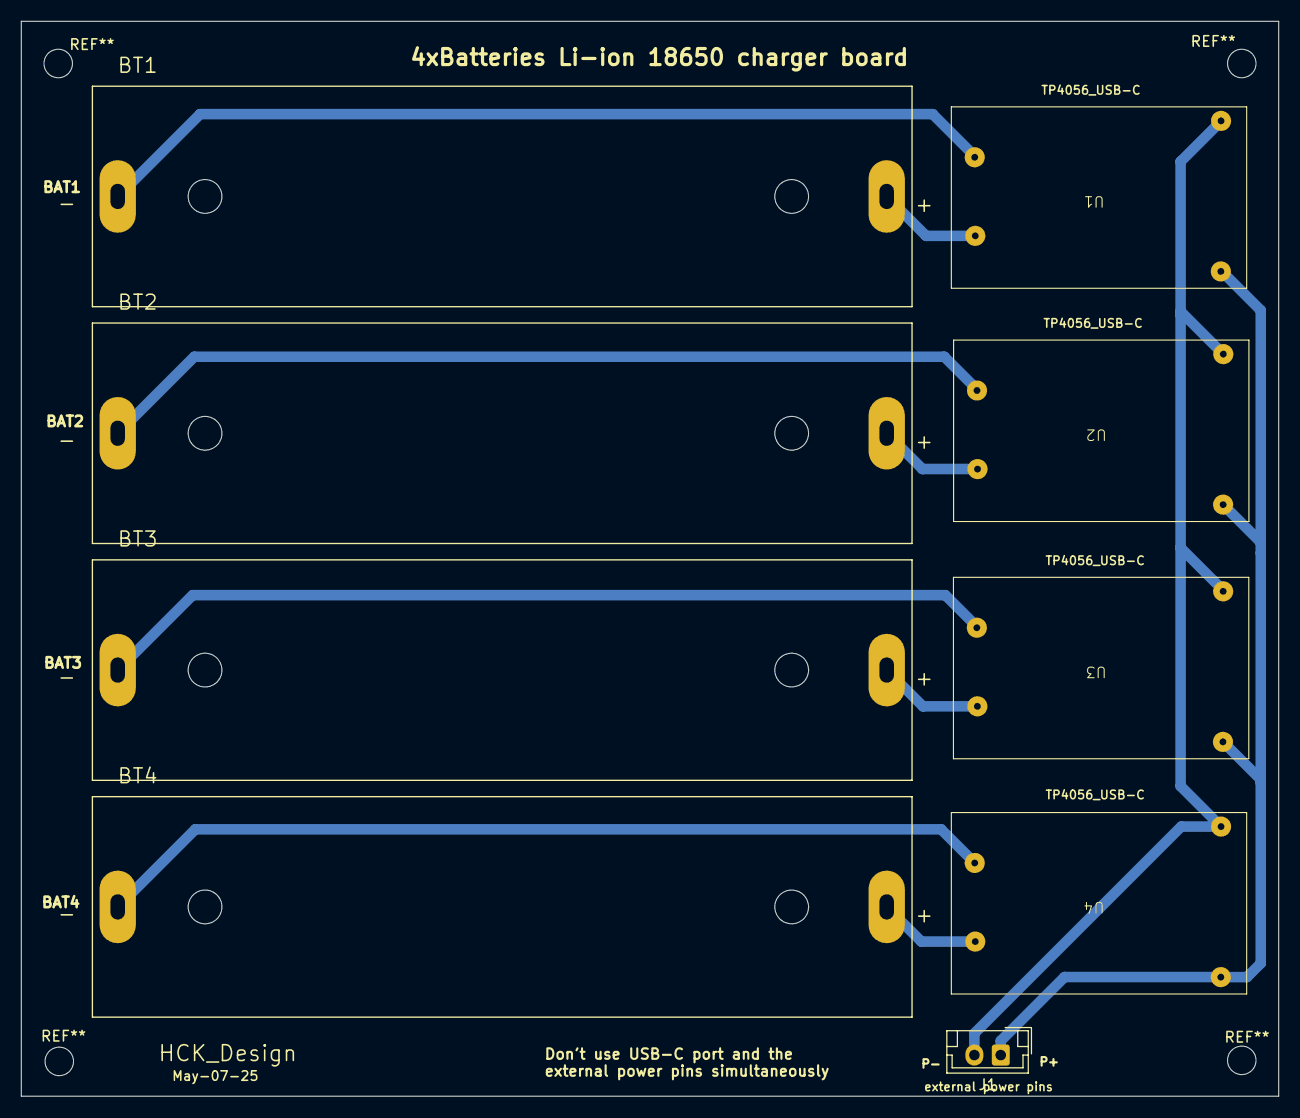
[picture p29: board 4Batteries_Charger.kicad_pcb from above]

Board: 2 copper layers, 119.2 x 101.9 mm, 9 parts (0 on the bottom side), 10 nets.

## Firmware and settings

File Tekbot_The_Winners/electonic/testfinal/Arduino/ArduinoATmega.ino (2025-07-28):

#include <Arduino.h>
#include <SoftwareSerial.h>
#include <Wire.h>
#include <Adafruit_TCS34725.h>
#include <math.h>

// Initialisation du capteur TCS34725
Adafruit_TCS34725 tcs = Adafruit_TCS34725(TCS34725_INTEGRATIONTIME_50MS, TCS34725_GAIN_4X);

#define MOTOR_DIR 4
#define MOTOR_PULSE	5
#define MOTOR_ENABLE 15
#define batteryPin A0
#define laser1 16
#define laser2 17
long step_time = 250;
int numColors = 4;

SoftwareSerial esp01(7, 6); // RX, TX vers ESP8266

volatile int count_depart = 0;
volatile int count_fin = 0;

bool tapis_en_marche = false;
unsigned long lastSent = 0;
const float ratio = 4.167;
String color;
long batteryCharge;
int increment = 0;

// Structure pour stocker les valeurs de référence
struct ColorRef {
  String name;
  float r_ref;
  float g_ref;
  float b_ref;
};

// Tableau des couleurs de référence 
ColorRef colors[] = {
  {"red", 0.489, 0.257, 0.254},
  {"green", 0.252, 0.417, 0.331},
  {"blue", 0.217, 0.406, 0.377},
  {"yellow", 0.367, 0.416, 0.217}
};

// === Interruptions ===
void departTapis() {
  //count_depart++;
  Serial.println("Faisceau début coupé !");
  tapis_en_marche = true;
  digitalWrite(13, HIGH); // Simule démarrage moteur
}

void finTapis() {
  //count_fin++;
  Serial.println("Faisceau fin coupé !");
  tapis_en_marche = false;
  digitalWrite(13, LOW); // Simule arrêt moteur
}




void senseBatteryCharge(){
  // simulatedBattery = 95 ;
  long sum = 0;
  for(int i=0; i<5; i++){
    sum += analogRead(A0);
  }
  batteryCharge = (ratio * map(sum/5, 0, 1023, 0, 4)*100)/16.8;
  Serial.println(batteryCharge);
}


String DetectedColor(){
  String detectedColor ;
  uint16_t r, g, b, c;
  float r_norm, g_norm, b_norm;

  // Lire les données brutes du capteur
  tcs.getRawData(&r, &g, &b, &c);

  // Normaliser les valeurs RVB
  float sum = r + g + b;
  if (sum == 0) sum = 1; // Éviter la division par zéro
  r_norm = r / sum;
  g_norm = g / sum;
  b_norm = b / sum;

  // Trouver la couleur la plus proche
  String detectedColor = "Inconnue";
  float minDistance = 1500.0; // Valeur initiale élevée
  for (int i = 0; i < numColors; i++) {
    // Calculer la distance euclidienne
    float distance = sqrt(
      pow(r_norm - colors[i].r_ref, 2) +
      pow(g_norm - colors[i].g_ref, 2) +
      pow(b_norm - colors[i].b_ref, 2)
    );
       if (distance < minDistance) {
        minDistance = distance;
        detectedColor = colors[i].name;
    }
   
  }

  // Vérifier le seuil de distance et l'intensité lumineuse
  if (minDistance > 0.3 || c < 900) {
    detectedColor = "Inconnue ";
  }

  return detectedColor;

}

void light_led(String color){
  if(color == "red"){
    digitalWrite(9, HIGH); delay(500); digitalWrite(9, LOW);
  }
  else if(color == "blue"){
    digitalWrite(11, HIGH); delay(500); digitalWrite(11, LOW);
  }
  else if(color == "green"){
    digitalWrite(12, HIGH); delay(500); digitalWrite(12, LOW);
  }
  else if(color == "yellow"){
    digitalWrite(10, HIGH); delay(500); digitalWrite(10, LOW);
  }
  else {
    digitalWrite(9, LOW);  //delay(200);
    digitalWrite(10, LOW); //delay(200);
    digitalWrite(11, LOW); //delay(200);
    digitalWrite(12, LOW); //delay(200);
  }
}

void setup() {
  Serial.begin(9600);
  if (tcs.begin()) {
    Serial.println("Capteur TCS34725 détecté !");
  } else {
    Serial.println("Erreur : capteur TCS34725 non détecté. Vérifiez les connexions !");
    //while (1); // Boucle infinie en cas d'erreur
  }
  pinMode(2, INPUT);  // Faisceau départ
  pinMode(3, INPUT);  // Faisceau fin
  pinMode(13, OUTPUT); // LED moteur simulé
  pinMode(8, OUTPUT);       digitalWrite(8, HIGH);
  //esp01.begin(9600);

	pinMode(MOTOR_DIR, OUTPUT);       digitalWrite(MOTOR_DIR, LOW);
	pinMode(MOTOR_PULSE, OUTPUT);	 		digitalWrite(MOTOR_PULSE, LOW);
	pinMode(MOTOR_ENABLE, OUTPUT); 		digitalWrite(MOTOR_ENABLE, HIGH);
  // Serial.println("Moto");
  attachInterrupt(digitalPinToInterrupt(2), departTapis, RISING);
  attachInterrupt(digitalPinToInterrupt(3), finTapis, RISING);

  digitalWrite(13, LOW);
  Serial.println("Système de tri initialisé.");

  pinMode(9, OUTPUT);       digitalWrite(9, LOW);  //delay(200);
  pinMode(10, OUTPUT);      digitalWrite(10, LOW); //delay(200);
  pinMode(11, OUTPUT);      digitalWrite(11, LOW); //delay(200);
  pinMode(12, OUTPUT);      digitalWrite(12, LOW); //delay(200);

  pinMode(laser1, OUTPUT);      digitalWrite(laser1, HIGH);
  pinMode(laser2, OUTPUT);      digitalWrite(laser2, HIGH);
}

void loop() {
  digitalWrite(MOTOR_ENABLE, HIGH);
	if(tapis_en_marche){
    delay(250);
    digitalWrite(MOTOR_ENABLE, LOW);
    Serial.println(tapis_en_marche);
    while(tapis_en_marche){
      digitalWrite(MOTOR_PULSE, HIGH);    delayMicroseconds(step_time);
      digitalWrite(MOTOR_PULSE, LOW);     delayMicroseconds(step_time);
    }
    digitalWrite(MOTOR_ENABLE, HIGH);
    delay(200);
    color = DetectedColor();
    senseBatteryCharge();
    delay(250);
    // Envoie des données collectées.
		String data = color + "#" + String(batteryCharge);
    esp01.println(data);
    delay(25);
    while(!esp01.available()){}

    if(esp01.available()){
      delay(100);
      String data = esp01.readStringUntil('\n');
      Serial.print("Réponse ESP : ");
      Serial.println(data);
      delay(20);    esp01.flush();    
    }
    delay(150);
    light_led();
  }
	else return ;
}

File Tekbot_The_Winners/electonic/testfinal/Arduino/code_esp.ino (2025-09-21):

#include <Arduino.h>
#include <ESP8266WiFi.h>
#include <ESP8266HTTPClient.h>

// === Configuration Wi-Fi ===
// const char* ssid = "Fruc S10+";
// const char* password = "obtne20220";

// const char* ssid = "Moov -Africa";         // Remplacez par le nom de votre réseau Wi-Fi
// const char* password = "@@password@"; // Remplacez par le mot de passe de votre réseau Wi-Fi

const char* ssid = "rasptank";         // Remplacez par le nom de votre réseau Wi-Fi
const char* password = "azerty1234"; // Remplacez par le mot de passe de votre réseau Wi-Fi

// === Configuration du serveur Flask ===
const char* flaskServerHost = "192.168.100.21";
const int flaskServerPort = 5000;

String color, batteryLevel, data;
String apiEndpoint = "";

unsigned long previousMillis = 0;
const long interval = 2000;  // Intervalle d’envoi

void setup() {
  Serial.begin(9600);
  delay(100);
  //Serial.println("ESP démarrage...");

  WiFi.begin(ssid, password);
  //Serial.print("Connexion au Wi-Fi");

  int retries = 0;
  while (WiFi.status() != WL_CONNECTED && retries < 50) {
    delay(500);
    //Serial.print(".");
    retries++;
  }

  if (WiFi.status() == WL_CONNECTED) {
    Serial.println("Connected");
  }
  else {
    Serial.println(" X not Connected"); 
  }
}

void loop() {
  if (!Serial.available()) return;
  if (Serial.available()) {
		delay(100);
    data = Serial.readStringUntil('\n');
    Serial.println("D");

    // --- Envoyer la requête HTTP GET ---
    WiFiClient client;
    HTTPClient http;
    // Traitement de la donnée
    int sep = data.indexOf('#');
    if (sep > 0) {
      color = data.substring(0, sep);
      batteryLevel = data.substring(sep + 1);

      // Construire l'URL complète
      apiEndpoint = "/api/set?color=" + color + "&battery=" + String(batteryLevel);

      String serverPath = "http://" + String(flaskServerHost) + ":" + String(flaskServerPort) + String(apiEndpoint);
      //Serial.println(serverPath);
      if (http.begin(client, serverPath)) {  // HTTP
        int httpCode = http.GET();
        // httpCode will be negative on error
        if (httpCode > 0) {
          Serial.printf("code: %d\n", httpCode);   //Serial.print(httpCode);
          delay(50);    Serial.flush();
          if (httpCode == HTTP_CODE_OK || httpCode == HTTP_CODE_MOVED_PERMANENTLY) {
            String payload = http.getString();
          }
        }
      } 
      else {}
      http.end();
    } 
    else {//Serial.printf("[HTTP] Unable to connect\n");
    }
  }
}

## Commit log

2025-06-18 Ajout du dossier Tekbot_The_Winners
    [piece1.SLDPRT, piece2.SLDPRT, piece3.SLDPRT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]
2025-06-18 Ajout 2 du dossier Tekbot_The_Winners
    [Axe de biellette.SLDPRT, Axe de porte machoire.SLDPRT, Biellette.SLDPRT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]
2025-06-18 Mise à jour 2 du dossier Tekbot_The_Winners
    [piece3.SLDPRT, piece4.SLDPRT]
2025-06-22 Mise à jour
    [Assemblage 2_a.SLDASM, Assemblage 2_b.SLDASM, Partie 2.SLDPRT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]
2025-06-28 Mise à jour du dossier Tekbot_The_Winners
    [TEST3_Cas_1.SLDPRT, TEST3_Cas_2.SLDPRT, TEST3_Cas_3.SLDPRT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]
2025-07-28 Ajout fichier
    [4Batteries_Charger.kicad_pcb, 4Batteries_Charger.kicad_sch, Test_convoyeur.kicad_pcb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]
2025-09-21 ajout de zip
